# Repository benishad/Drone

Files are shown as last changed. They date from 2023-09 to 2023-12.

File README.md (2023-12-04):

## ✈️드론의 비행 거리를 늘려보자[중계 통신 드론 프로젝트]
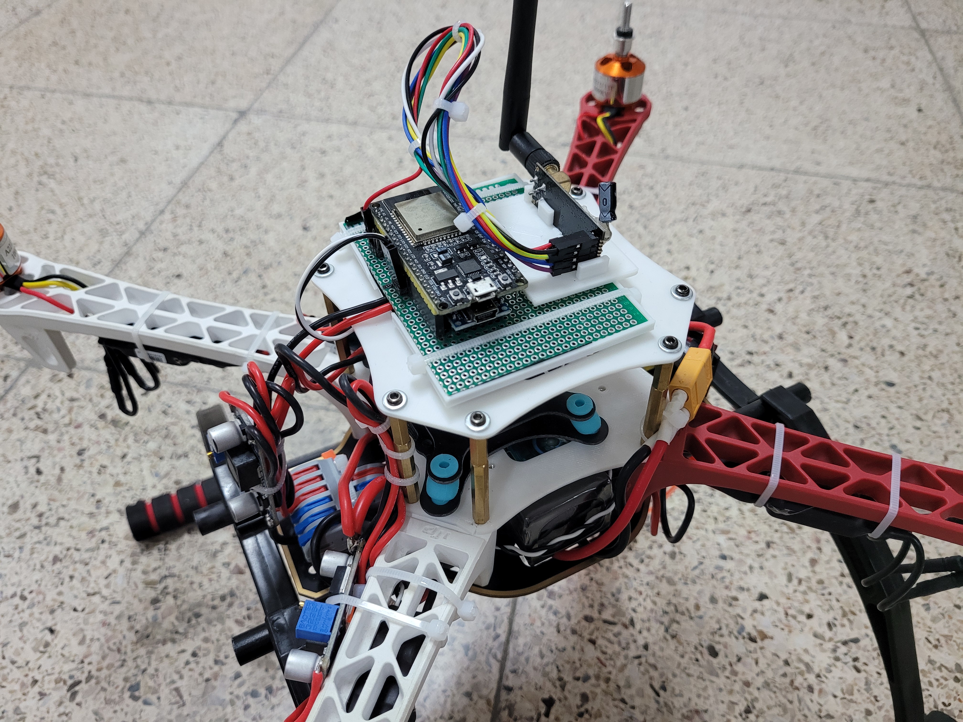
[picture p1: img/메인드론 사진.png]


## 중계 통신 드론이란?

- **중계 드론**은 일반 학생들이 저렴하게 드론을 제작하고 SW코딩 학습과 더불어 드론의 비행 거리를 늘리는데 목적이 있습니다.

- 중계 통신을 이해하기 쉬운 예는 휴대전화 입니다. 저희가 상대방과 전화를 할 수 있는 이유는 기지국이 중계소 역할을 해주는 덕분입니다.

- 조종기와 드론 사이에 중계소 역할을 하는 드론을 제작하는 것이 중계 드론 프로젝트 입니다.

- 드론 시뮬레이터를 제작하여 문서에서 제작한 조종기를 사용하여 드론 조종 훈련이 가능합니다.

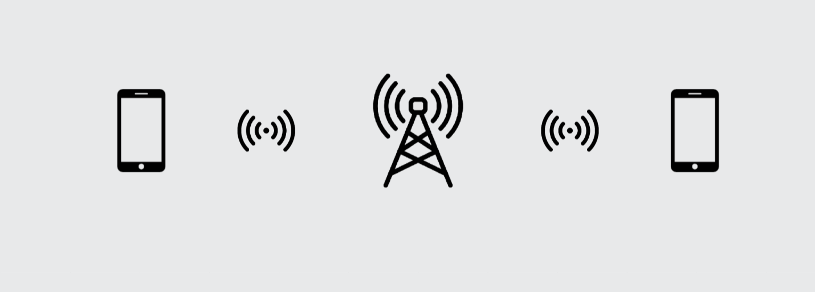
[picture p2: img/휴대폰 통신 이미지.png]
휴대폰_통신_이미지 휴대전화 통신 방식
<br>

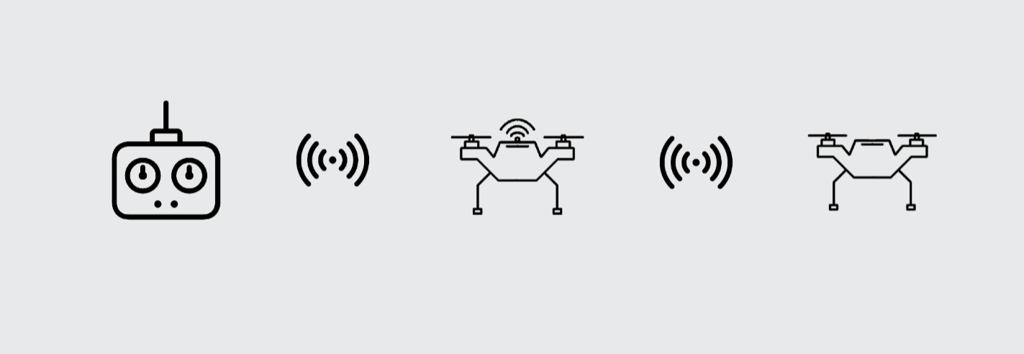
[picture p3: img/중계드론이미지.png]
중계드론이미지 중계 통신 드론 방식


## 바로가기
1. [중계 통신 드론이란?](#중계-통신-드론이란)

2. [바로가기](#바로가기)
    - [준비물](#준비물)
    - [회로도](#회로도)
    - [드론 제작에 앞서](#드론-제작에-앞서)
    - [제작 과정](#제작-과정)
    - [문서](#문서)

3. [중계 드론 빌드 방법 PDF](https://drive.google.com/file/d/1Zqlsaz8OV26cVhaoOtoAvIVqaOmRjo3B/view?usp=sharing)

4.  [드론 시뮬레이터 다운로드](https://drive.google.com/file/d/1ymEPB1GEQYfEJyJiITfJfxDNSJ_VvF2R/view) 설정 방법은 문서를 참고
 
<br>

## 준비물
>준비물 예시 입니다. 방식만 같거나 비슷하다면 다른 더욱 좋은 솔루션이 있을 수 있습니다.

### 준비
- ESP32 **(필수)**
- ATmega328 **(필수)**
- Nrf24l01 **(필수)**
- 10μF커페시터(안전성을 높여줍니다.)
- GY-521(MPU6050) **(필수)**
- 스텝다운 모듈 혹은 레귤레이터
- 조이스틱 혹은 조종기(조종기는 내부를 제거하고 조이스틱을 사용합니다. 고장난 조종기를 추천) **(필수)**
- 토글 스위치 **(필수)**
- 헤더 핀 소켓
- 3mm 인서트 너트
- 진동 방지용 댐퍼 **(필수)**
- F450 드론 프레임 **(필수)**
- 모터와 ESC (ESC용량에 주의해 주세요.) **(필수)**
- 배터리와 프롭 **(필수)**

혹은 다른 프레임을 준비해도 괜찮습니다. 또한, 폴더에 F450 규격에 프레임 출력 파일이 있습니다. 높은 추력과 효율을 위해서는 모터, 배터리, 프롭을 고려해 알맞은 제품을 구해야 합니다. **문서에서는 효율에 대한 내용을 다루지 않습니다.**

<br>

## 회로도
  >회로는 조종기, 중계 드론, 메인 드론 3가지 입니다.

### 조종기
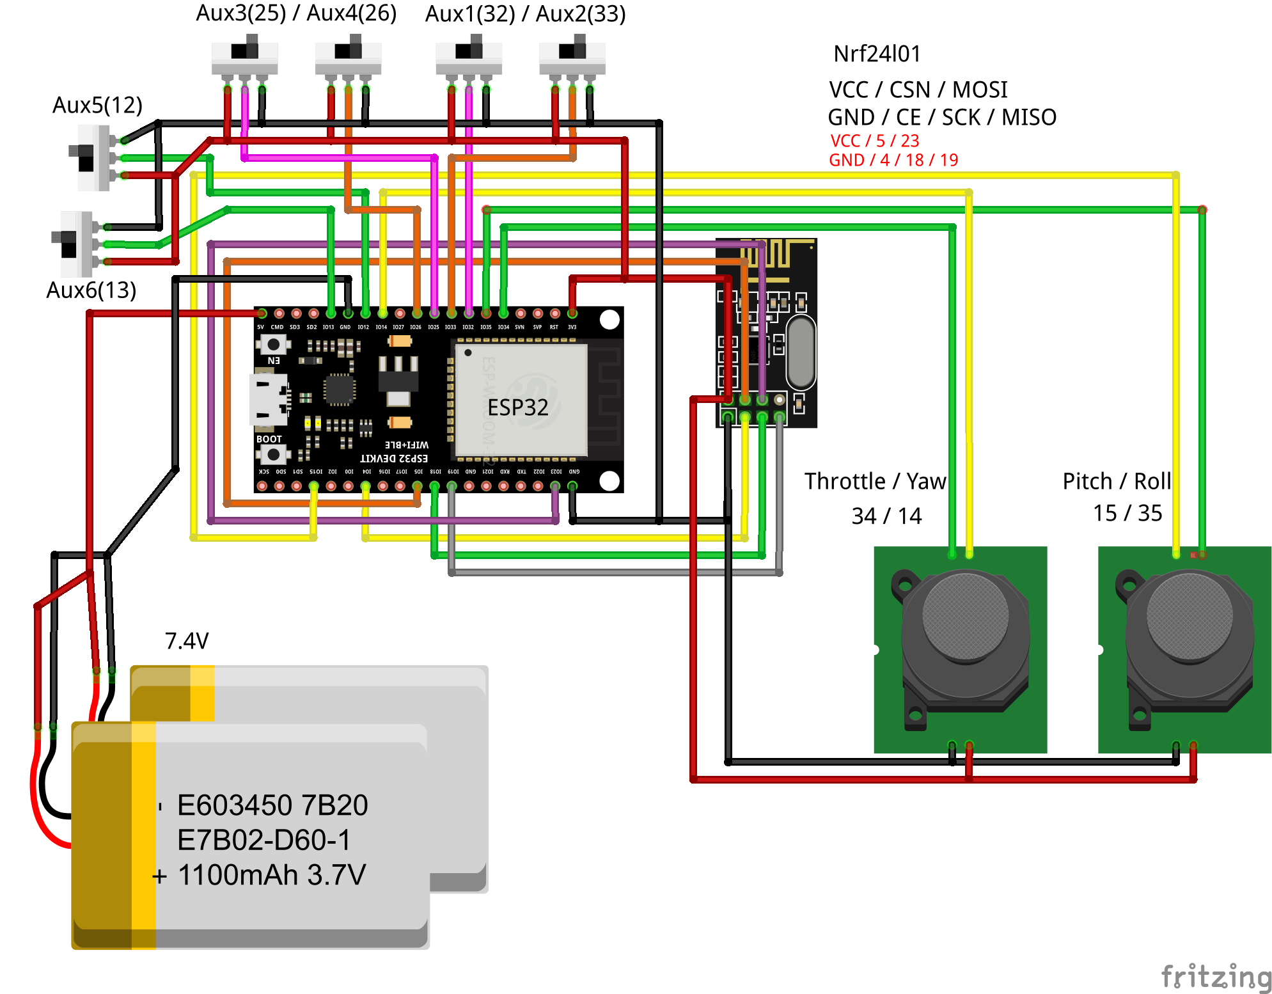
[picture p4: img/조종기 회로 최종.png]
조종기_회로 조종기 회로
<br>

### 중계 드론
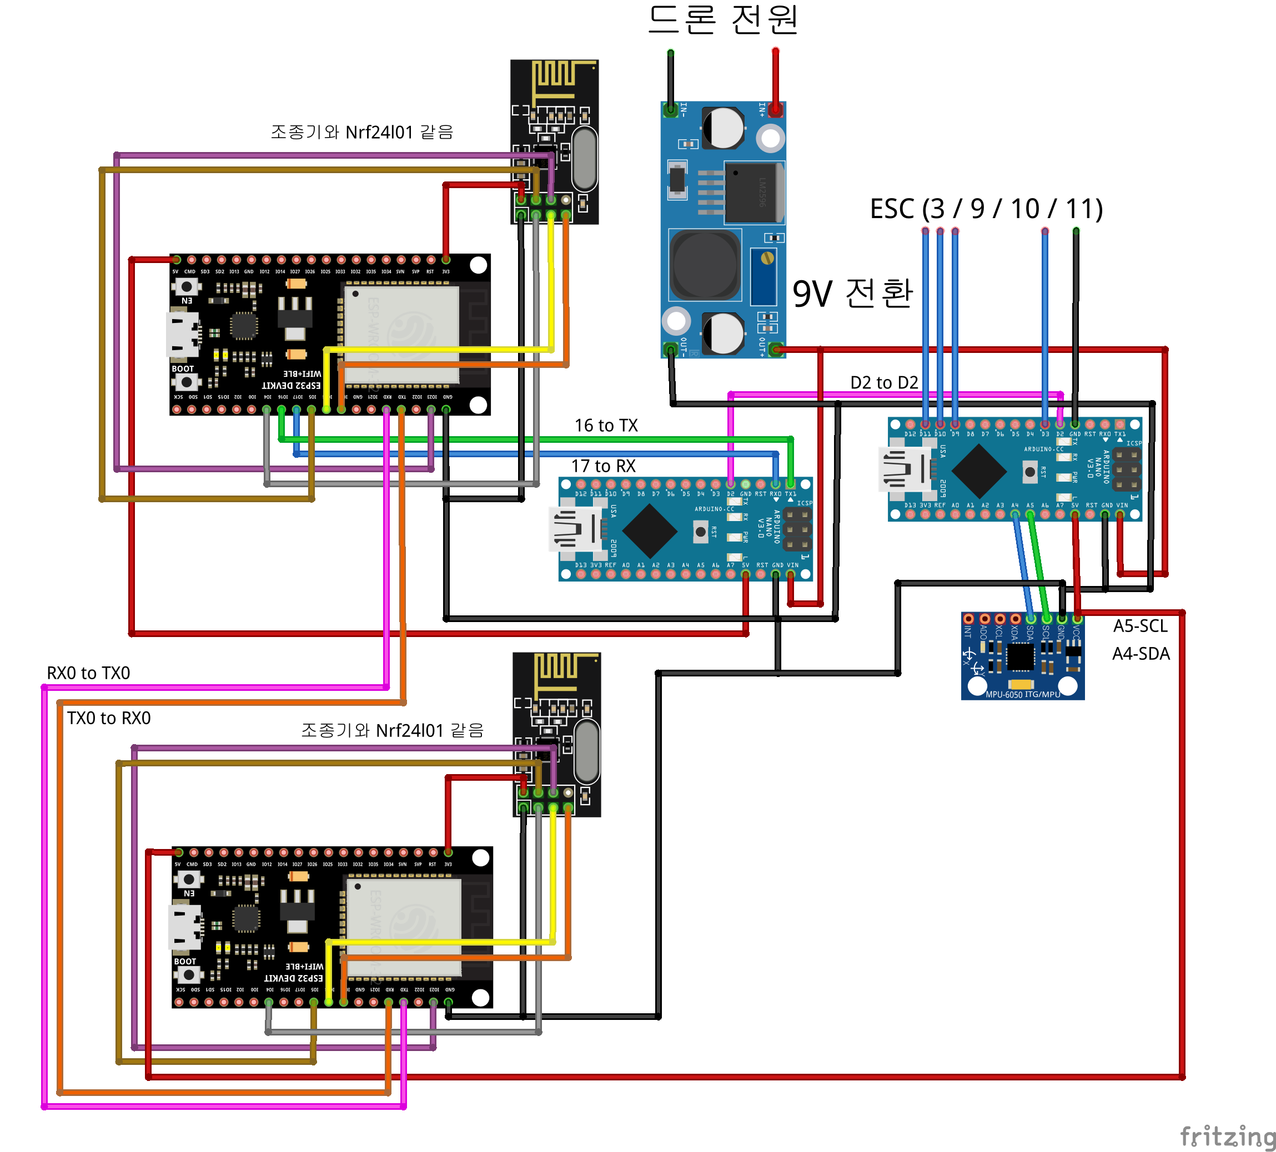
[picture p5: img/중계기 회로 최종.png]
중계기_회로 중계기 회로
<br>

### 메인 드론
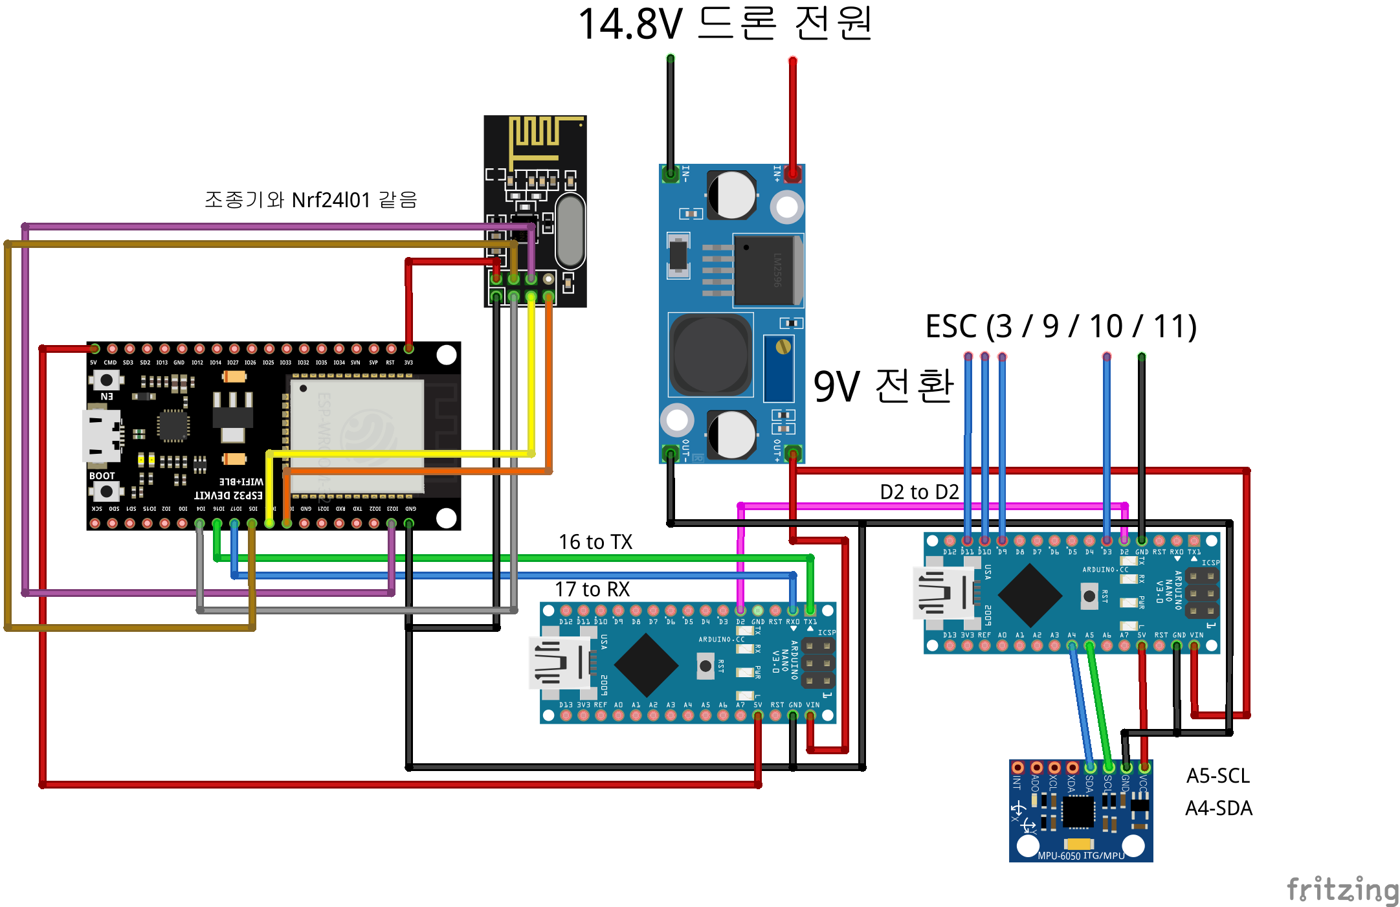
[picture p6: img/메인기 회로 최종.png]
<br>

### 시뮬레이터 수신기
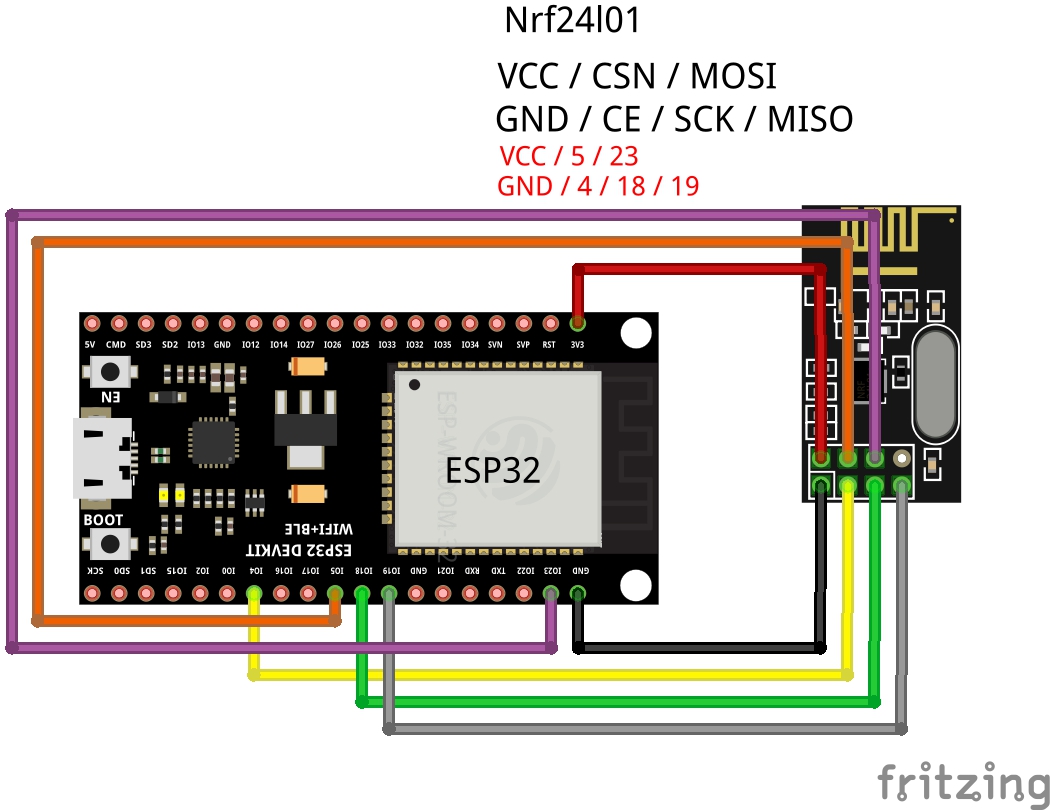
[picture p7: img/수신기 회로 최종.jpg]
<br>
수신기는 위에 제작한 중계 드론과 메인 드론 회로와 동일합니다. 따라서 두 드론 중 하나를 사용하여 소스코드를 업로드하는 것으로 시뮬레이터 수신기로 사용이 가능합니다.

<br>

## 드론 제작에 앞서
  - ### 전압 분배
    ESP32와 아두이노 보드 전원공급을 드론 배터리로 해결 합니다. 따라서 드론의 14.8V 혹은 다른 용량의 배터리 전압을 낮춰줄 필요가 있습니다. 위 회로에서는 9V로 정하였지만 **사용하는 보드에 입력 전압을 숙지하고 그에 맞춰서 조정**하길 바랍니다.
  <br>
  <br>
  배터리 전원은 ESC, ESP32, 아두이노 등으로 전달 되어야 하기에 적절한 분배 장비를 이용해야 합니다.<br><br>
  
&nbsp;&nbsp;&nbsp;&nbsp;&nbsp;&nbsp;&nbsp;&nbsp;&nbsp;&nbsp;- 전원 분배 보드

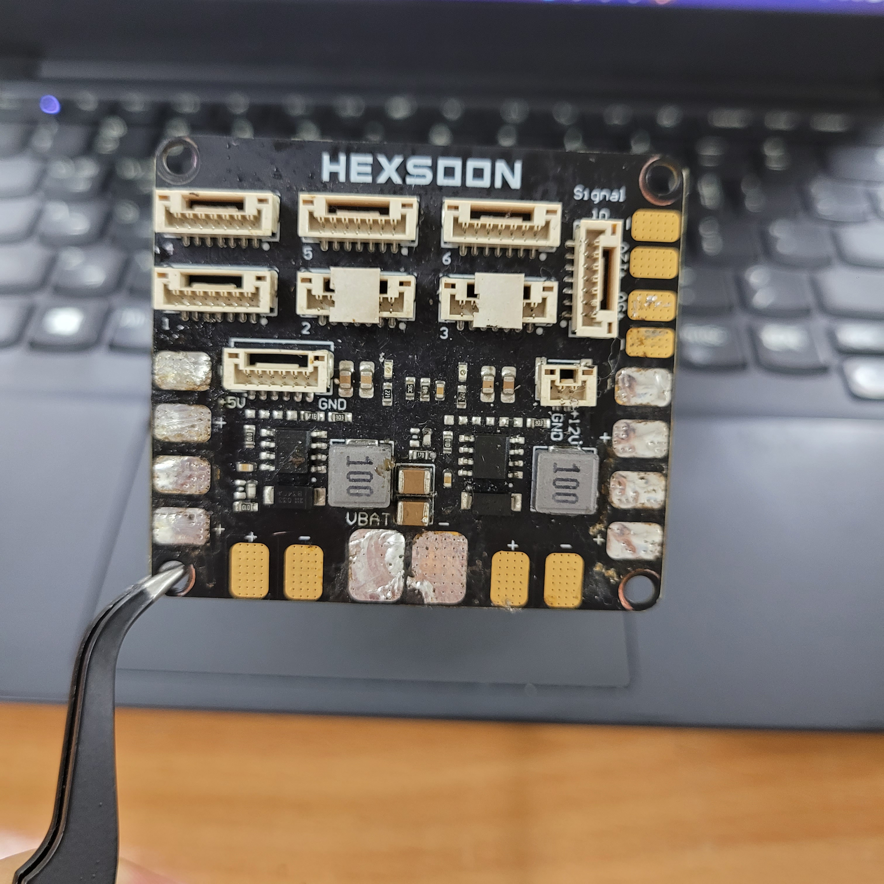
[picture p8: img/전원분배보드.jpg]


  &nbsp;&nbsp;&nbsp;&nbsp;&nbsp;&nbsp;&nbsp;&nbsp;&nbsp;&nbsp;- 바디 전원 분배

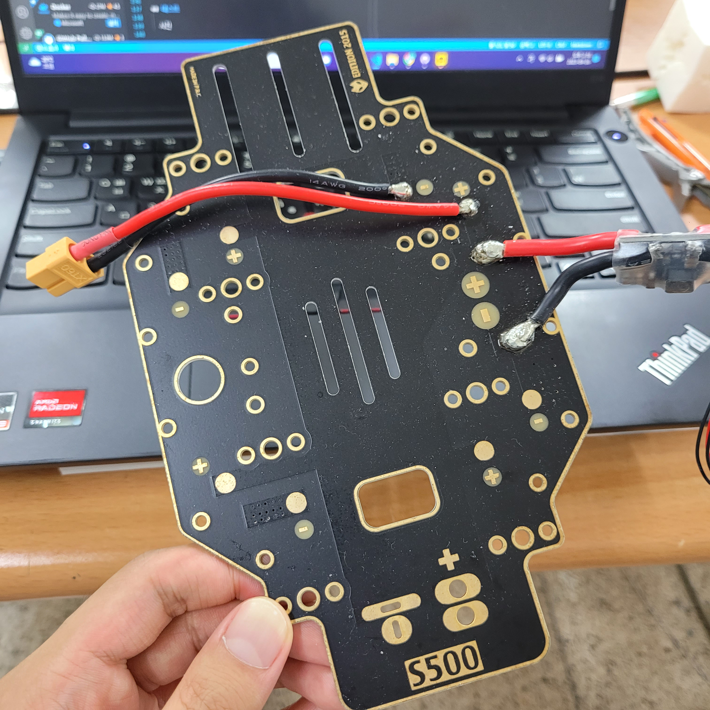
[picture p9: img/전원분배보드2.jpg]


  &nbsp;&nbsp;&nbsp;&nbsp;&nbsp;&nbsp;&nbsp;&nbsp;&nbsp;&nbsp;- 기타 등등...

  - ### 전압 조정
    전압 조정 방법 또한 여러 방법이 있습니다.
    <br>
    BEC, 레귤레이터, 스텝다운 등등..
    <br>
    이 문서에서는 스텝다운 모듈을 사용하여 전압을 낮추어 아두이노 보드에 입력합니다.<br>
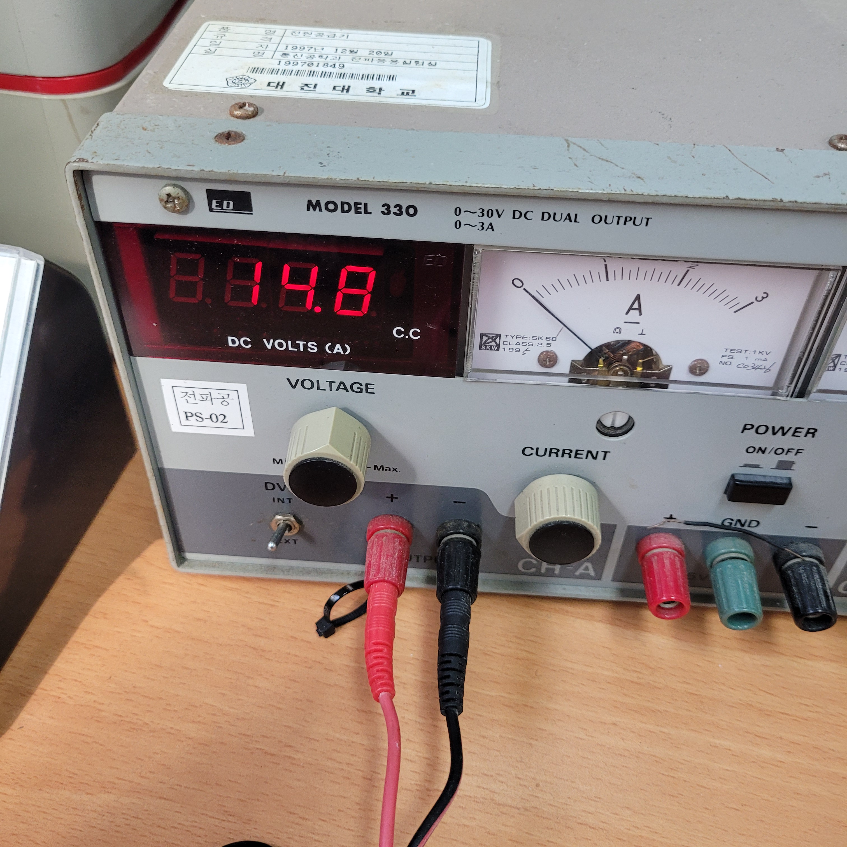
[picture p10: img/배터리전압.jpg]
    <br>

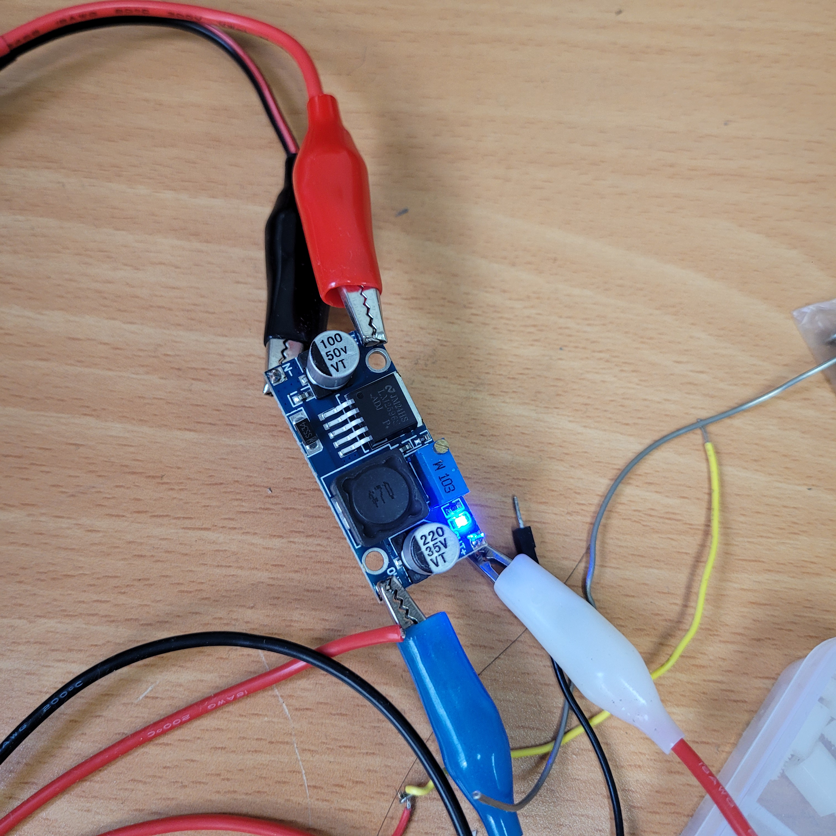
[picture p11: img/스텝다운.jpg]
    <br>

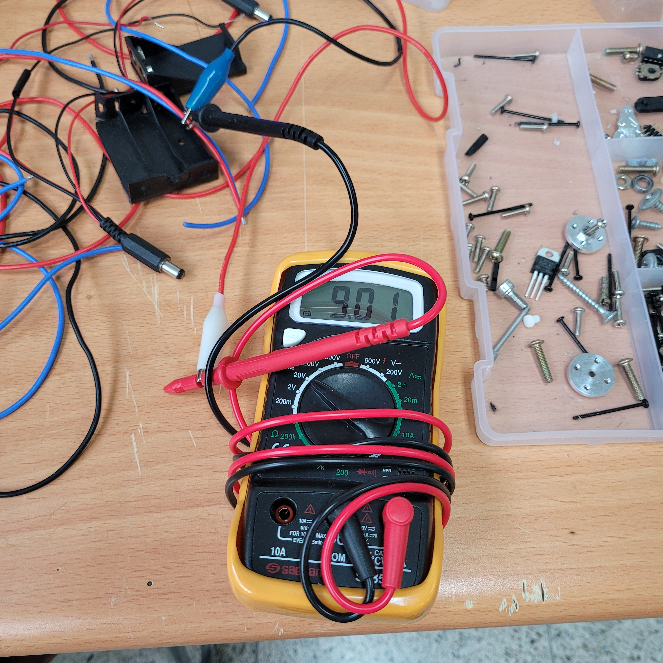
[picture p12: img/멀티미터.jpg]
    
  
  <br>

  - ### Multiwii
    Multiwii는 드론 제작에 많이 사용되는 FC(Flight Controller) 소프트웨어입니다.
    Multiwii는 오픈 소스 프로젝트로서, 사용자들이 자유롭게 소스 코드를 수정하거나 개선할 수 있습니다. 개인적인 프로젝트부터 상업적인 제품까지, 다양한 범위에서 사용될 수 있습니다.<br>
    아래 링크를 통해 Multiwii를 다운로드하여 사용합니다.
  <br>
  <br>

    [Multiwii 다운로드](http://www.multiwii.com/) 바로가기

  <br>
  <br>
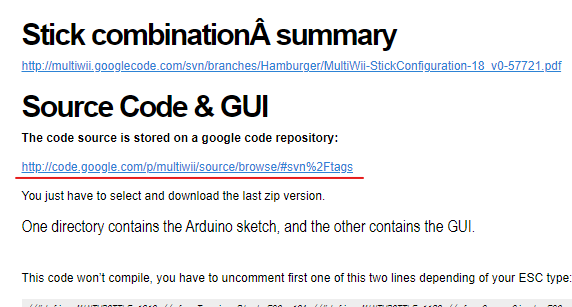
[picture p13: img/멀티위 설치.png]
  <br><br>

## 제작 과정

  - ### ESP32와 Nrf24l01 10μF커패시터 납땜
    >필수는 아니지만 편의성과 안정성을 위해서 진행하는 것을 추천합니다.<br>

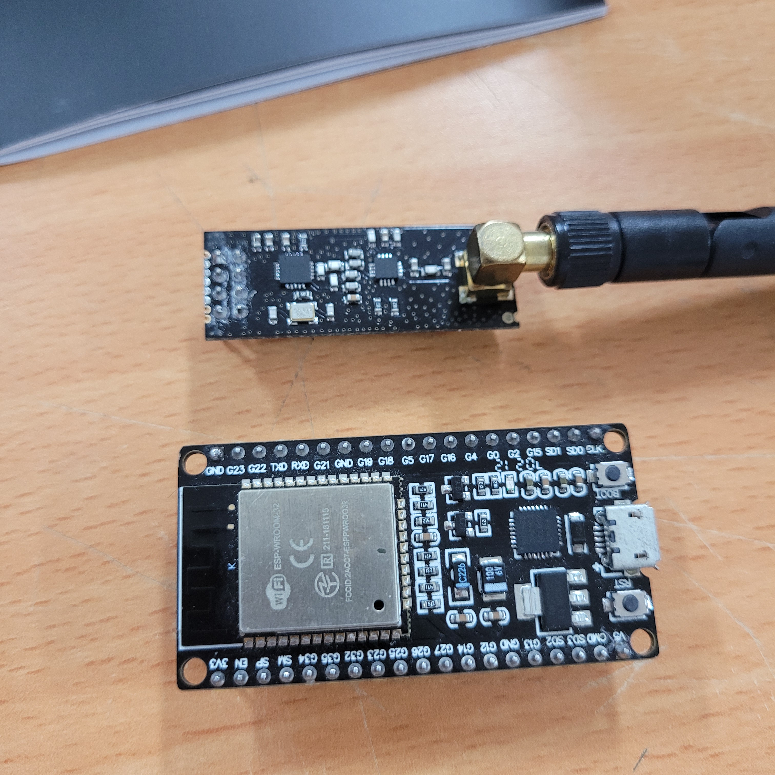
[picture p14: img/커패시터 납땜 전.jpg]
    <br>

    - 커패시터 납땜 위치를 확인하세요.
    - ESP32 EN 단자와 GND를 연결해야 합니다.<br>

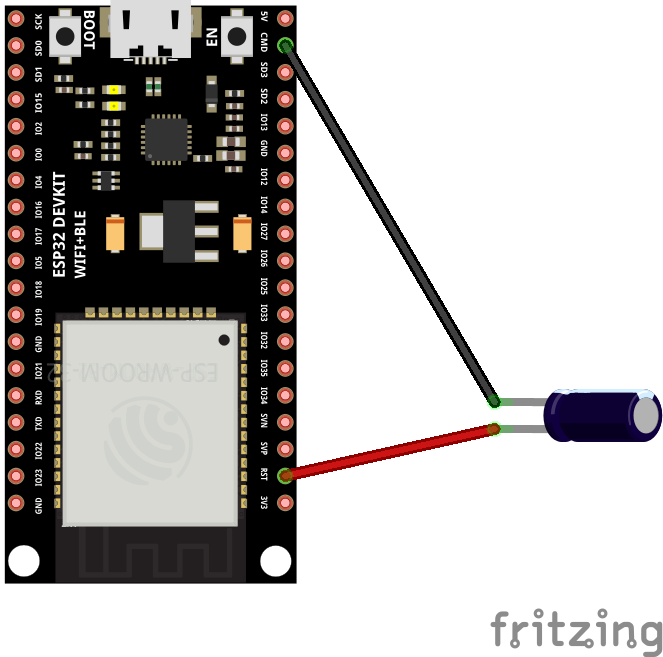
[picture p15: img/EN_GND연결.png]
    <br>

    - 위 처럼 연결해도 괜찮지만 너무 단자가 길어집니다. 여기서는 아래와 같이 직접 연결을 하여 공간을 최소화 하겠습니다.<br>

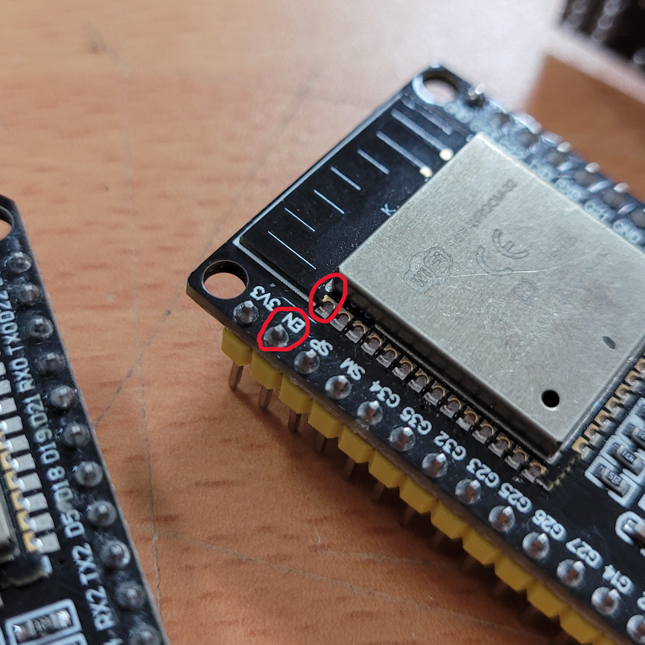
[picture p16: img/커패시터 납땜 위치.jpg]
    <br>

    - 커패시터 단자 + - 를 확인하세요.<br>

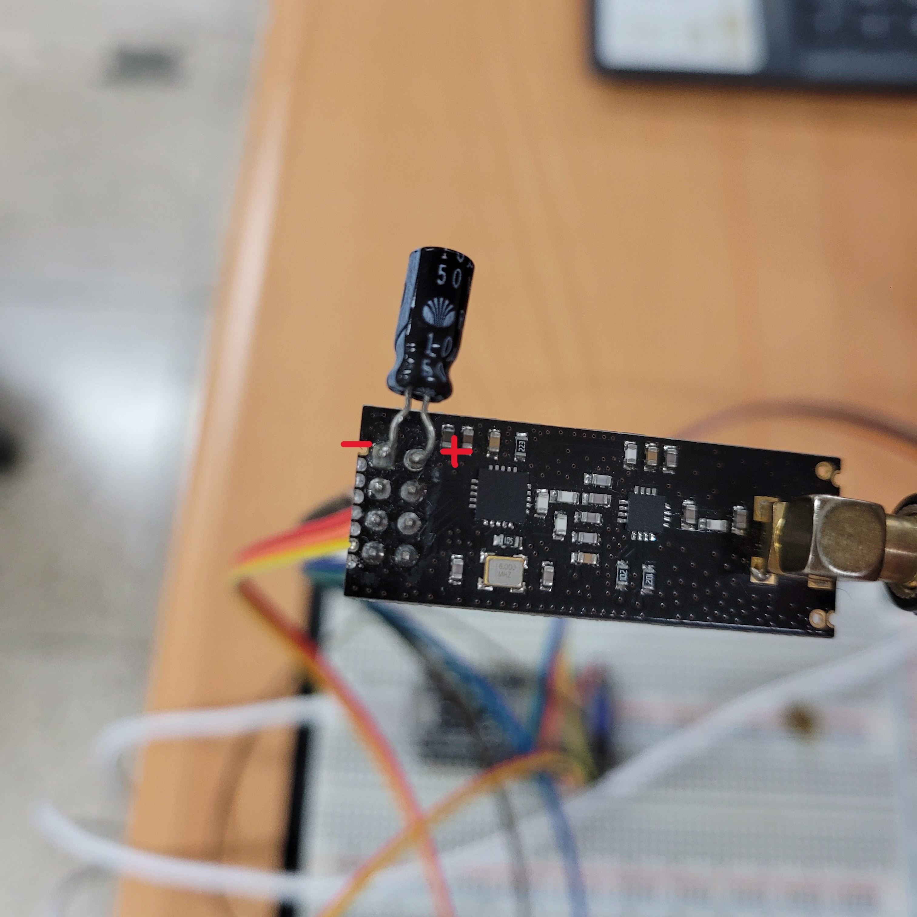
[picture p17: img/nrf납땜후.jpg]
    <br>
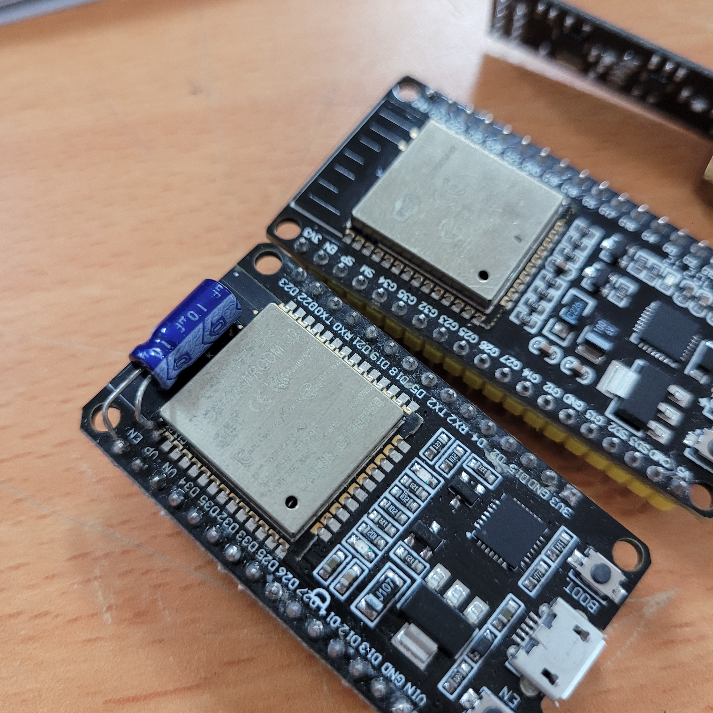
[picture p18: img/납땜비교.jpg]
    <br>

    - 위 와 같은 모습을 만들었으면 성공입니다. 다시 언급하지만 위와 똑같이 진행 할 필요는 없습니다.<br>

  - ### 조종기 제작
    
    조종기 제작은 두 가지 방법이 있습니다.

    1. 실제 조종기 혹은 고장난 조종기 기판을 제거하고 사용하기.

    2. 브레드보드 혹은 만능기판에 회로를 구성하여 사용하기.

    회로도를 위에 게시해 두었으니 회로 제작은 넘어가겠습니다.
    아래는 제작된 조종기 두 가지 버전입니다.

    #### 조종기 ver.1
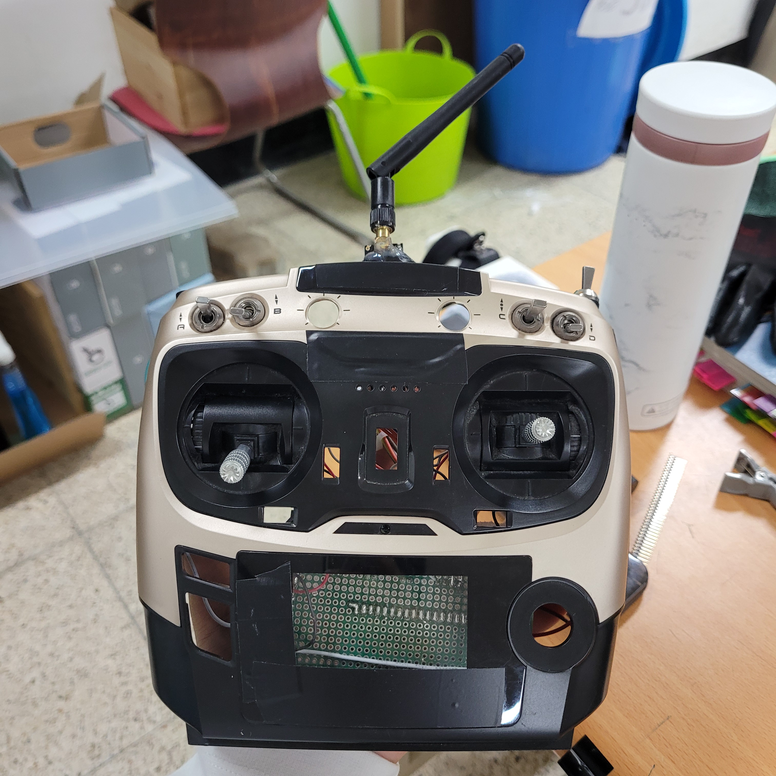
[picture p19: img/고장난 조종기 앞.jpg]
    <br>

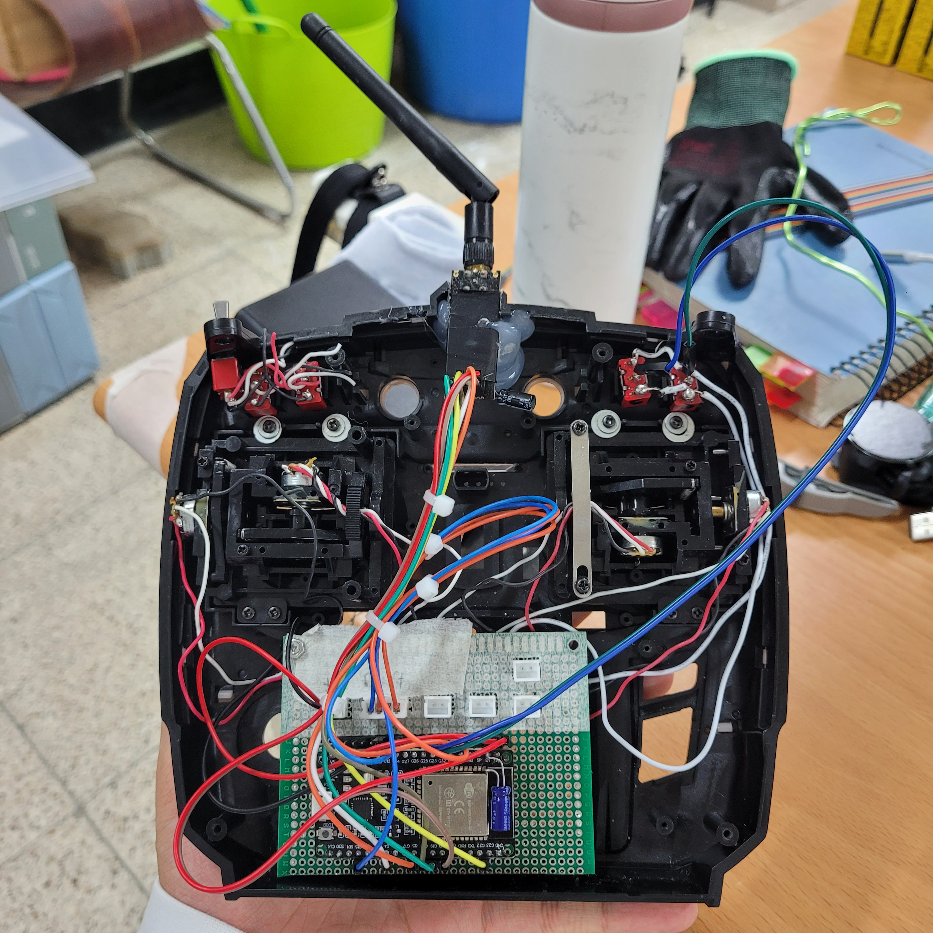
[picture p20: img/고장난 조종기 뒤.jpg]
    <br>

    #### 조종기 ver.2
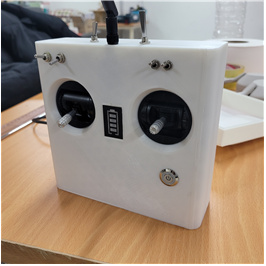
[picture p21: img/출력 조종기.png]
    <br>

  - ### MPU6050 설치 과정
    mpu6050은 수평을 유지시키기 위한 핵심 부품 입니다. 비행시 mpu6050에 문제가 생기지 않게 댐퍼와 출력물을 사용해 mpu6050을 고정해야 합니다.

    재료를 준비합니다.<br>
    CAD폴더에서 mpu6050 관련 출력물을 출력해 사용합니다. 직접 설계하거나 다른 방법을 사용해도 괜찮습니다. **mpu6050에 이상이 생기지 않게 하는 작업임을 인지해 주세요.**

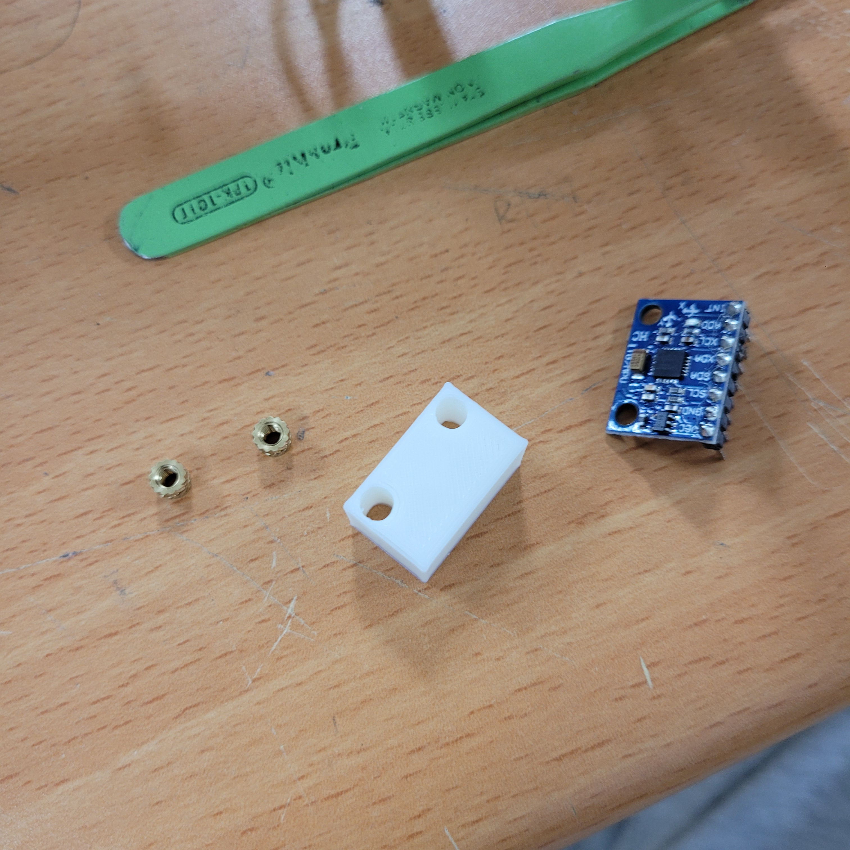
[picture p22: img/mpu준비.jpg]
    

    ※ 해당 출력물은 헤더소켓을 끼웠을 때 고정되는 길이로 제작되었습니다.<br>
    인서트 너트를 넣고 조립 준비를 합니다.

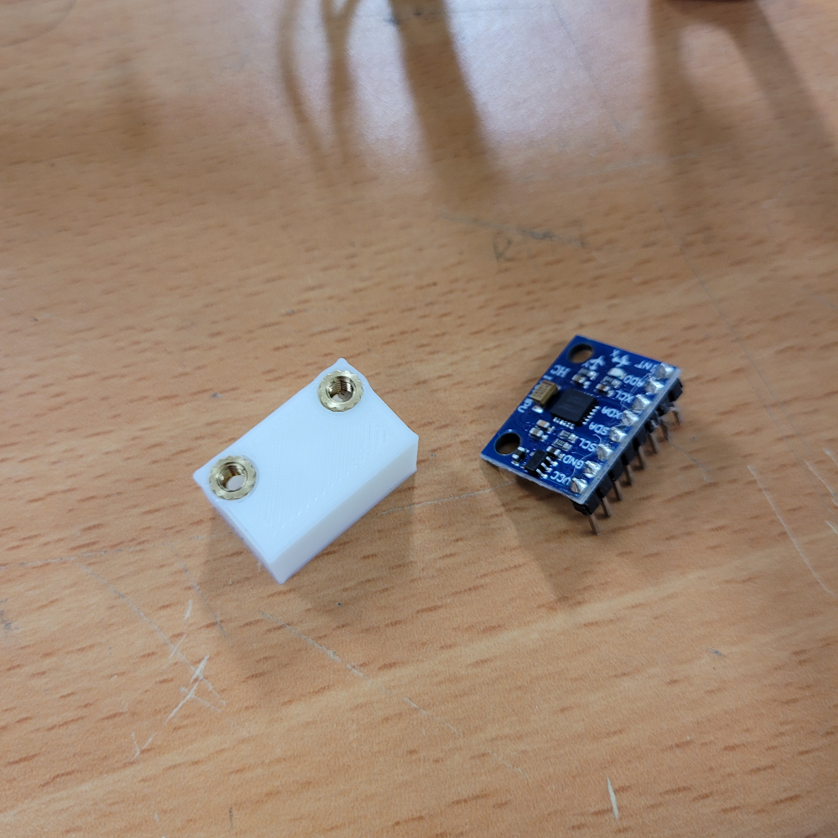
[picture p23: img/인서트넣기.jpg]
    

    비행시 생기는 진동에 대비하도록 댐퍼 위에 mpu6050을 설치하여 마무리 합니다.

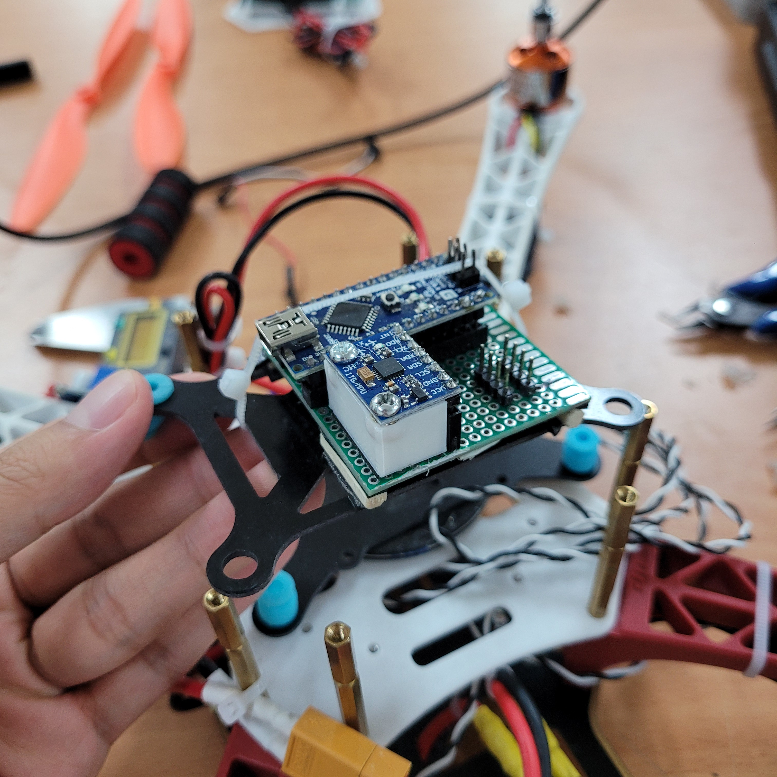
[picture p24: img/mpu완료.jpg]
    

<br>

## 문서

  이후 모든 작업에 대한 설명은 아래 문서에 기술

[중계 드론 빌드 방법 PDF](https://drive.google.com/file/d/1Zqlsaz8OV26cVhaoOtoAvIVqaOmRjo3B/view?usp=sharing)

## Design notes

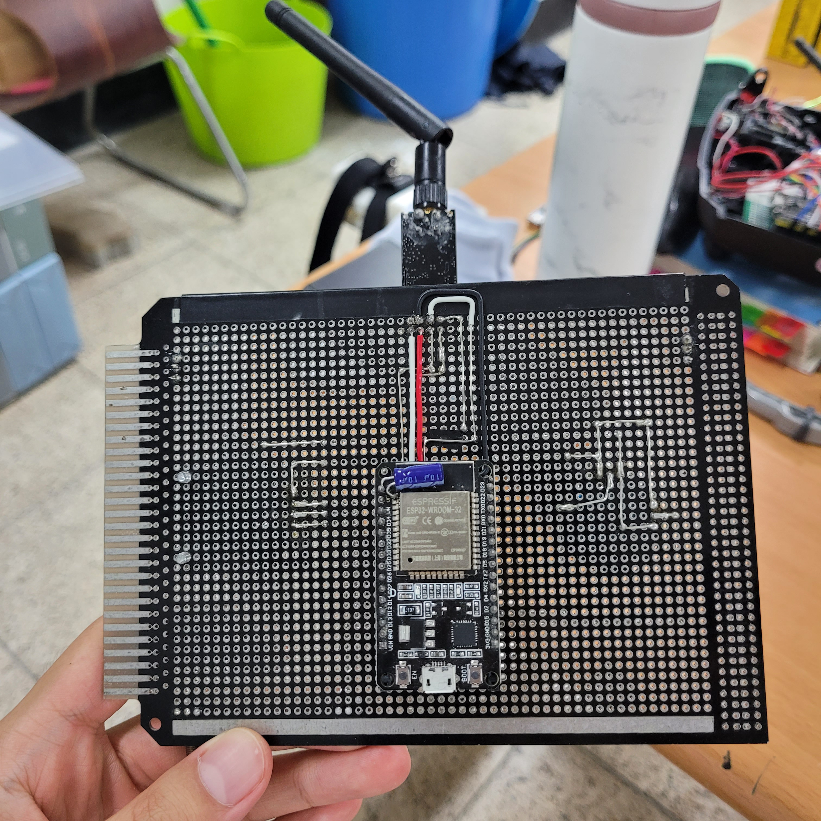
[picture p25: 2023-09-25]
img/기판 조종기 뒤.jpg

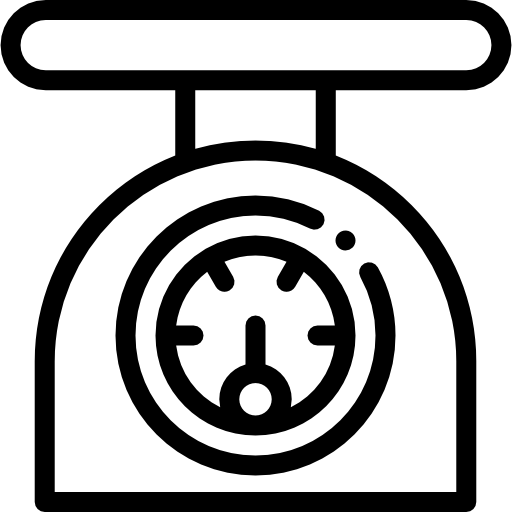
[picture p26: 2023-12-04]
img/무게.png

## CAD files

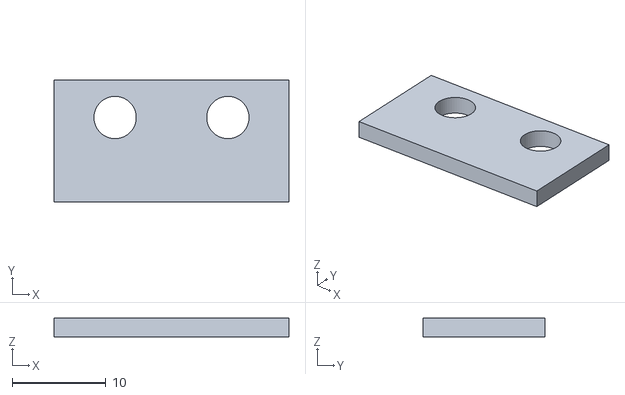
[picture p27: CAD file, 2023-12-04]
CAD/락피스.stl
25.0 x 13.0 x 2.00

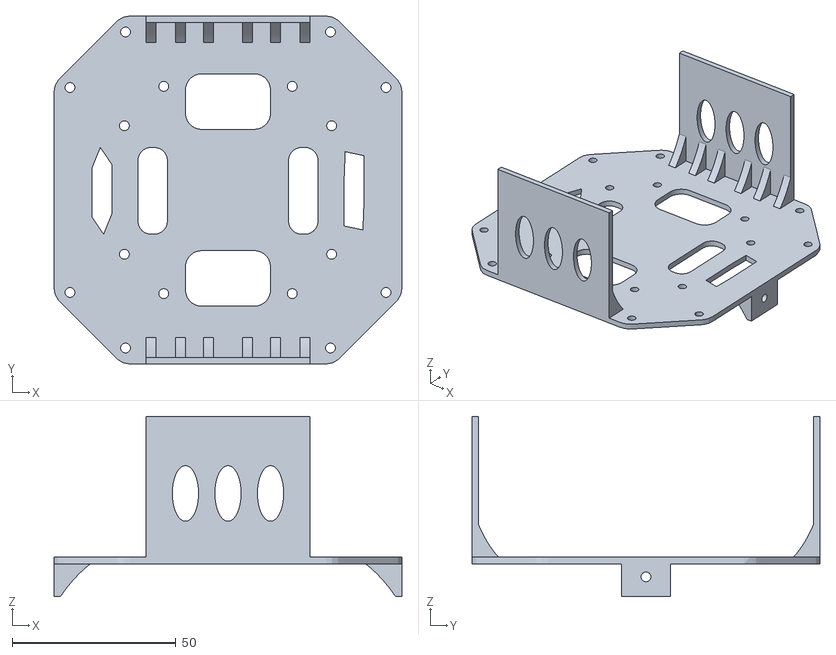
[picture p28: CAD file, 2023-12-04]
CAD/Drone_DOWN.stl
106.3 x 106.3 x 55.0

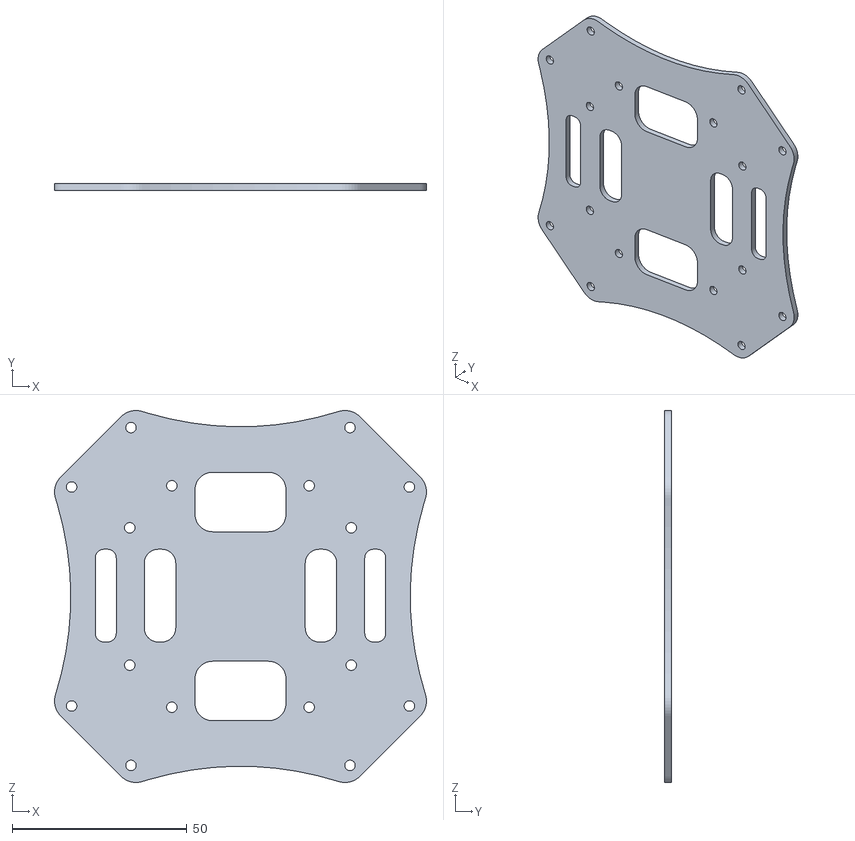
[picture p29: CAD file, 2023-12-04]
CAD/드론 top.STL
106.3 x 2.00 x 106.3

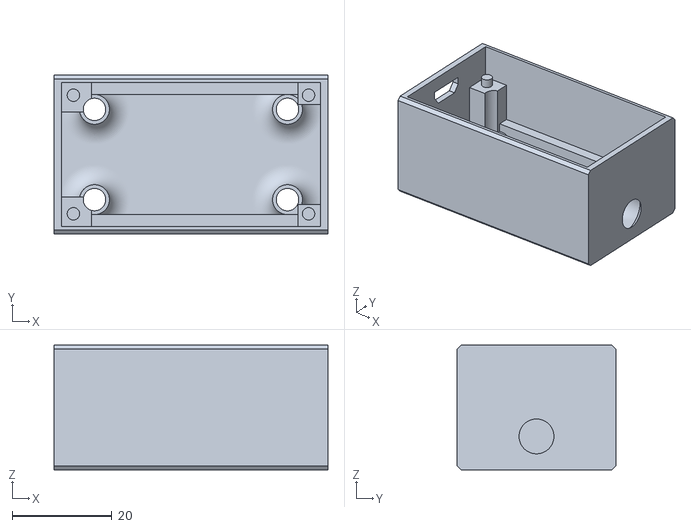
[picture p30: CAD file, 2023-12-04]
CAD/Nrf_Body.stl
55.0 x 32.0 x 25.0

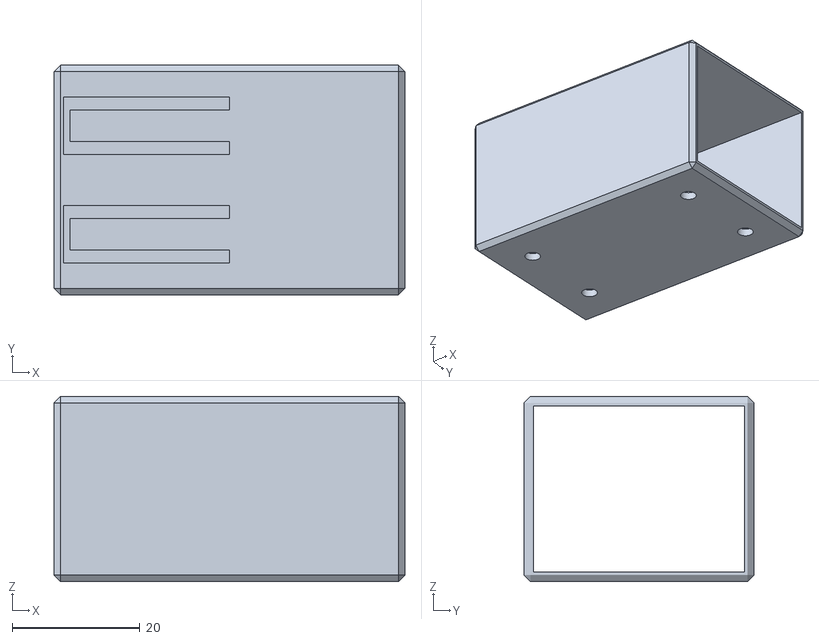
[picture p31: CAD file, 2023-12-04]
CAD/Nrf_Head.stl
55.0 x 36.0 x 29.0

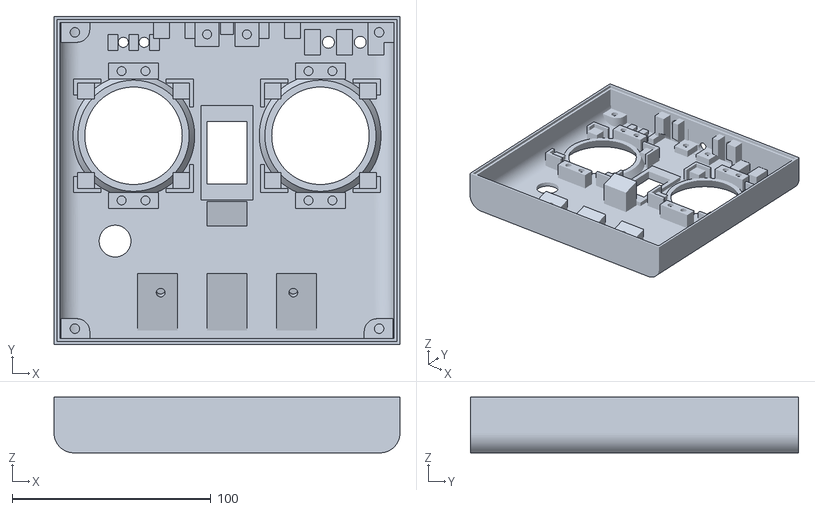
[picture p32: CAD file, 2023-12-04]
CAD/조종기.stl
174.0 x 165.0 x 28.0

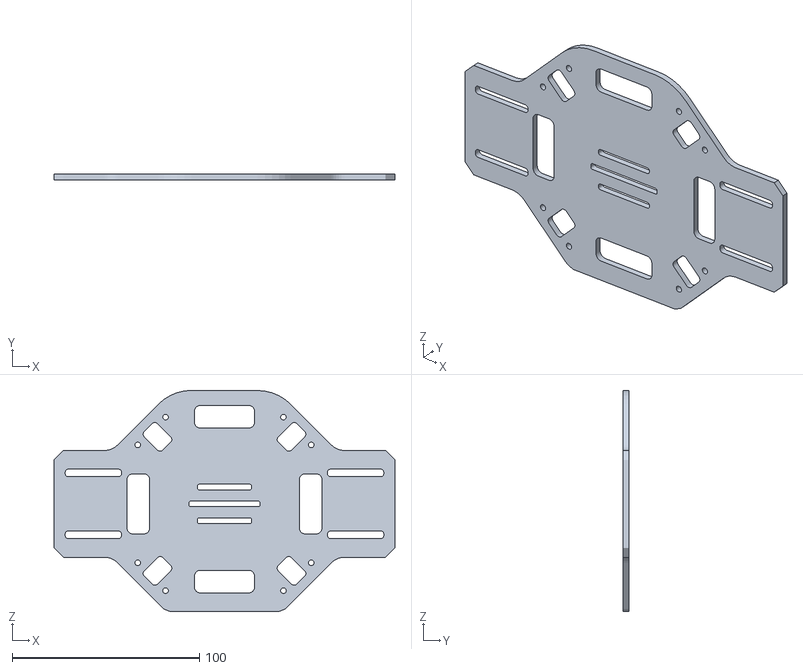
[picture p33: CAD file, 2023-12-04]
CAD/드론 bottom.STL
182.0 x 3.00 x 118.1

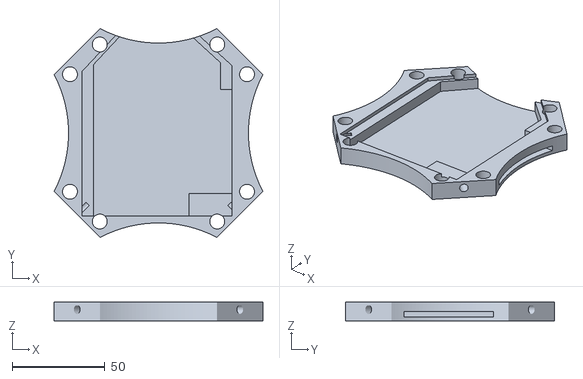
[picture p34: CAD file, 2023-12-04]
CAD/중계드론기판_하단.stl
112.4 x 112.4 x 10.0

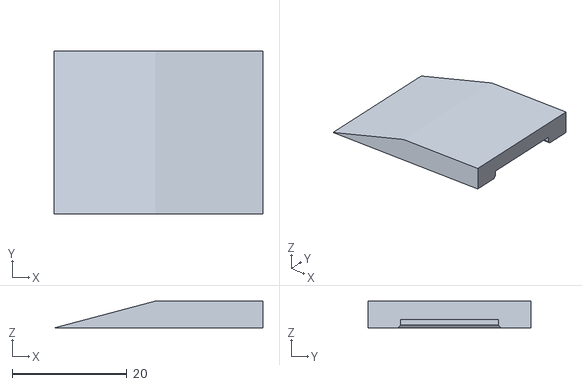
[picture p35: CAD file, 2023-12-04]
CAD/bracket.stl
36.4 x 28.4 x 4.70

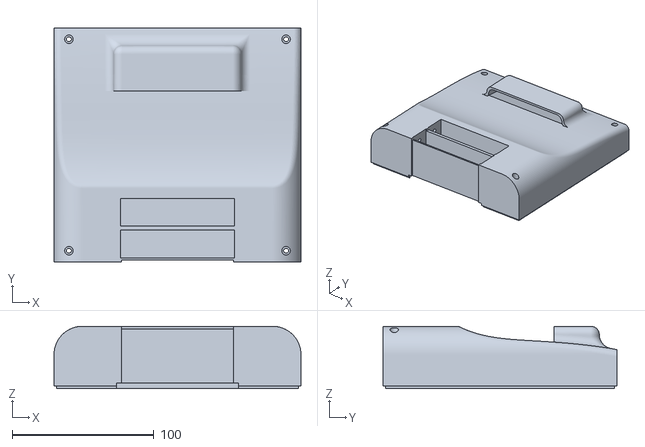
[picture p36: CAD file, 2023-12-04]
CAD/조종기 플레이트.stl
174.0 x 165.0 x 44.0

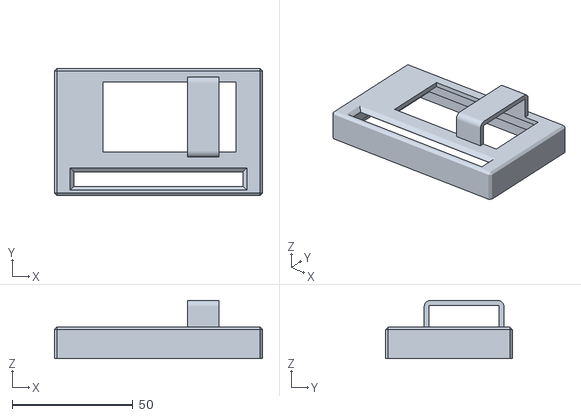
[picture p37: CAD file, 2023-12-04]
CAD/메인 드론 케이스_1.stl
86.0 x 52.5 x 24.0

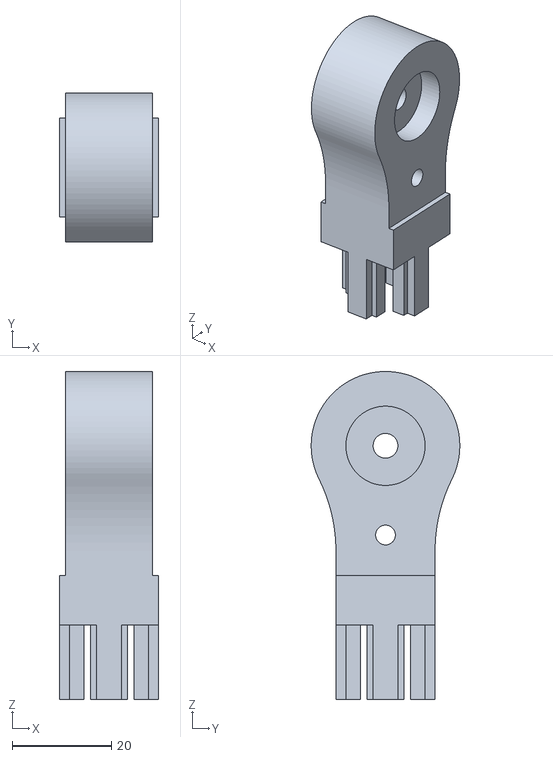
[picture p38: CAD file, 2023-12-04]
CAD/수평계 마운트.stl
20.0 x 30.0 x 66.2

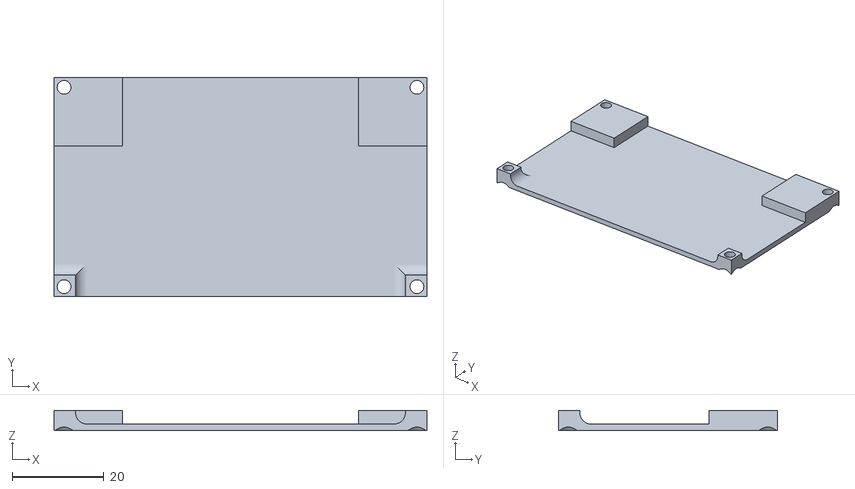
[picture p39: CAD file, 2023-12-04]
CAD/메인 드론 케이스_2.stl
81.4 x 47.9 x 4.45

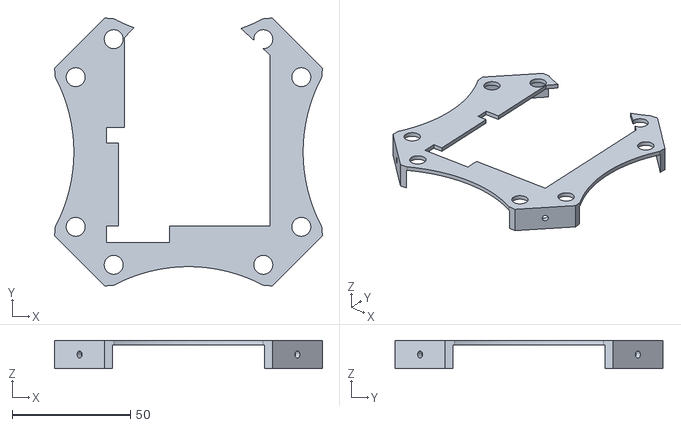
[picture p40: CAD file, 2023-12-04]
CAD/중계드론기판_상판.stl
113.1 x 113.1 x 12.0

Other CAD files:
CAD/수평계.stl
CAD/Drone_UP.stl
CAD/nrf24_hw.stl
CAD/mpu_leg.stl

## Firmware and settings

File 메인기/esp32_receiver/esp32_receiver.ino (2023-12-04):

//////////////////////////////////////////////////////////////////////////////////
//메인 드론
//중계통신으로 받은 값으로 작동하는 메인 드론 ESP32.
//받은 값을 처리하여 다시 나노로 전송하는 역할을 한다.
#include <SPI.h>
#include <RF24.h>

#define RXp2 16   //uart통신을 위한 핀
#define TXp2 17   //uart통신을 위한 핀

//long long pipeIn = 0x1234ABCDEFLL;   //주소값 설정
const uint64_t pipeIn = 0x5A1B2C3D4E5F6A7BLL;

char buf[10]; //  

RF24 radio(4, 5); // GPIO18 for CE, GPIO5 for CSN

bool communicationActive = true;  // 통신 활성화 상태
unsigned long lastCommunicationTime = 0;
unsigned long communicationTimeout = 5000;  // 통신 타임아웃 시간 (5초)

// 안전한 착지를 위한 Roll, Pitch, Yaw 값
const byte safeRoll = 128;
const byte safePitch = 128;
const byte safeYaw = 128;
const byte safeAUX1 = 000;
const byte safeAUX2 = 001;
const byte safeAUX3 = 000;
const byte safeAUX4 = 000;
const byte safeAUX5 = 000;
const byte safeAUX6 = 001;

struct MyData {
  byte throttle;
  byte yaw;
  byte pitch;
  byte roll;
  byte AUX1;
  byte AUX2;
  byte AUX3;
  byte AUX4;
  byte AUX5;
  byte AUX6;
};

MyData receivedData;
MyData lastData;  // 마지막으로 받은 데이터를 저장할 변수

const int charge = 14;
const int fire = 12;

void setup() 
{
  Serial.begin(115200);
  Serial2.begin(9600, SERIAL_8N1, RXp2, TXp2);    //Atmega와 uart통신을 위한 시리얼
  radio.begin();
  radio.openReadingPipe(1, pipeIn); // Set the same address used in the transmitter
  radio.setDataRate(RF24_2MBPS);  // 데이터 전송 속도 설정
  // RF24_250KBPS, RF24_1MBPS, RF24_2MBPS
  //radio.setPALevel(RF24_PA_HIGH);
  //거리가 가까운 순으로 RF24_PA_MIN / RF24_PA_LOW / RF24_PA_HIGH / RF24_PA_MAX 등으로 설정
  radio.startListening(); //수신모드

  pinMode(charge, OUTPUT);
  pinMode(fire, OUTPUT);
}

void loop() 
{
  if (radio.available()) 
  {
    radio.read(&receivedData, sizeof(MyData));
    lastCommunicationTime = millis();  // 통신이 성공한 경우 타임아웃 타이머 재설정

    //============================================================
    //=====================메인 드론 개별 정지========================

    if(receivedData.AUX4 == 1) 
    {
      lastData.yaw = 127; // 중간값으로 설정
      lastData.pitch = 127;
      lastData.roll = 127;
      lastData.AUX1 = 0;
      lastData.AUX2 = 1;
      lastData.AUX5 = 0;
      lastData.AUX6 = 1;
      sendToNano(lastData);
      serial_print(lastData);
    } 
    else 
    {
      lastData = receivedData;  // 통신 데이터를 lastData에 저장
      sendToNano(receivedData);
      serial_print(receivedData);
    }
    
    //==============================================================
    //==============================================================

    //============================================================
    //===================== 코일건 발사 코드 ========================
    if(receivedData.AUX5 == 1)
    {
      Serial.println("- 충전 -");
      digitalWrite(charge, HIGH);
    }
    else if(receivedData.AUX5 == 0)
    {
      Serial.println("- 충전 꺼짐 -");
      digitalWrite(charge, LOW);
    }
    
    if(receivedData.AUX6 == 0)
    {
      digitalWrite(fire, HIGH);
      Serial.println("발사");
    }
    else if(receivedData.AUX6 == 1)
    {
      digitalWrite(fire, LOW);
      Serial.println("발사꺼짐");
    }
    //==============================================================
    //==============================================================
    
    communicationActive = true;
    delay(10);
  }
  
  //안전모드 동작부분
  else 
  {
    // 통신이 끊겼을 때의 동작
    if (communicationActive && (millis() - lastCommunicationTime >= communicationTimeout)) 
    {
      communicationActive = false;  // 통신 끊김 상태로 설정
      // 스로틀 값을 천천히 감소시켜 안전한 착지 모사
      for (int throttleValue = receivedData.throttle; throttleValue >= 0; throttleValue -= 2) 
      {
        Serial2.print("A");
        sprintf(buf, "%03d", throttleValue);
        Serial2.print(buf);
        Serial2.print("B");
        Serial2.print(safeYaw);  // 안전한 Yaw 값
        Serial2.print("C");
        Serial2.print(safePitch);  // 안전한 Pitch 값
        Serial2.print("D");
        Serial2.print(safeRoll);  // 안전한 Roll 값
        Serial2.print("E");
        sprintf(buf, "%03d", safeAUX1);
        Serial2.print(buf);
        Serial2.print("F");
        sprintf(buf, "%03d", safeAUX2);
        Serial2.print(buf);
        Serial2.println("G");
        delay(1000);  // 100ms 간격으로 스로틀 값을 감소시킴
      }
    }
  }
}

void sendToNano(MyData data) 
{
    Serial2.print("A");
    sprintf(buf, "%03d", data.throttle);
    Serial2.print(buf);
    Serial2.print("B");
    sprintf(buf, "%03d", data.yaw);
    Serial2.print(buf);
    Serial2.print("C");
    sprintf(buf, "%03d", data.pitch);
    Serial2.print(buf);
    Serial2.print("D");
    sprintf(buf, "%03d", data.roll);
    Serial2.print(buf);
    Serial2.print("E");
    sprintf(buf, "%03d", data.AUX1);
    Serial2.print(buf);
    Serial2.print("F");
    sprintf(buf, "%03d", data.AUX2);
    Serial2.print(buf);
    Serial2.println("G");
}
void serial_print(MyData data)
{
  Serial.print("메인기 =>  Throttle: ");
  Serial.print(data.throttle);
  Serial.print("  Yaw: ");
  Serial.print(data.yaw);
  Serial.print("  Pitch: ");
  Serial.print(data.pitch);
  Serial.print("  Roll: ");
  Serial.print(data.roll);
  Serial.print("  AUX1: ");
  Serial.print(data.AUX1);
  Serial.print("  AUX2: ");
  Serial.print(data.AUX2);
  Serial.print("  AUX3: ");
  Serial.print(data.AUX3);
  Serial.print("  AUX4: ");
  Serial.print(data.AUX4);
  Serial.print("  AUX5: ");
  Serial.print(data.AUX5);
  Serial.print("  AUX6: ");
  Serial.println(data.AUX6);
}

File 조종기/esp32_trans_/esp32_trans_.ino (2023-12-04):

//조종기 ESP32
//조종기에는 조이스틱 두개와 토글 스위치 5개, 푸쉬 버튼 1개가 설치됨
#include <SPI.h>
#include <RF24.h>

const uint64_t pipeOut = 0xABCD1234567890EFLL;  //주소값 설정

RF24 radio(4, 5); // 4번 ce 5번 csn

//조이스틱 핀 할당
const int THR = 34;
const int YAW = 14;
const int PITCH = 15;
const int ROLL = 35;
//각종 버튼 핀 할당
const int SW1 = 32;
const int SW2 = 33;
const int SW3 = 25;
const int SW4 = 26;
const int SW5 = 12;
const int SW6 = 13;

struct MyData {   //전송할 데이터 구조체 생성
  byte throttle;
  byte yaw;
  byte pitch;
  byte roll;
  byte AUX1;
  byte AUX2;
  byte AUX3;
  byte AUX4;
  byte AUX5;
  byte AUX6;
};

MyData data;

void resetData() 
{
  data.throttle = 0;
  data.yaw = 127;
  data.pitch = 127;
  data.roll = 127;
  data.AUX1 = 0;
  data.AUX2 = 0;
  data.AUX3 = 0;
  data.AUX4 = 0;
  data.AUX5 = 0;
  data.AUX6 = 0;
}

void setup()
{
  Serial.begin(115200);
  radio.begin();
  //radio.setAutoAck(false);
  //radio.setDataRate(RF24_250KBPS);
  // RF24_250KBPS, RF24_1MBPS, RF24_2MBPS
  //radio.setPALevel(RF24_PA_HIGH);
  //거리가 가까운 순으로 RF24_PA_MIN / RF24_PA_LOW / RF24_PA_HIGH / RF24_PA_MAX 등으로 설정
  radio.openWritingPipe(pipeOut);
  radio.stopListening(); // 송신모드
  resetData();

  pinMode(SW1, INPUT);    //angle 모드
  pinMode(SW2, INPUT);    //horizon 모드
  pinMode(SW3, INPUT);    //중계 단일 호버링 모드
  pinMode(SW4, INPUT);    //메인 단일 호버링 모드
  //응용 핀
  pinMode(SW5, INPUT);    //코일건 충전
  pinMode(SW6, INPUT);    //코일건 발사
}

/**************************************************/
//조이스틱에 중간 값이 조이스틱마다 저항 값에 차이가 있어서 그 값을 맞춰주는 함수
int mapJoystickValues(int val, int lower, int middle, int upper, bool reverse)
{
  val = constrain(val, lower, upper);
  if (val < middle)
    val = map(val, lower, middle, 0, 128);
  else
    val = map(val, middle, upper, 128, 255);
  return (reverse ? 255 - val : val);
}

void loop()
{
  data.throttle = mapJoystickValues(analogRead(THR), 260, 1890, 4030, false);
  data.yaw      = mapJoystickValues(analogRead(YAW), 0, 2077, 4095, true);
  data.pitch    = mapJoystickValues(analogRead(PITCH), 1179, 1776, 4095, true);
  data.roll     = mapJoystickValues(analogRead(ROLL), 0, 2061, 4095, false);
  data.AUX1     = digitalRead(SW1);
  data.AUX2     = digitalRead(SW2);
  data.AUX3     = digitalRead(SW3);
  data.AUX4     = digitalRead(SW4);
  data.AUX5     = digitalRead(SW5);
  data.AUX6     = digitalRead(SW6);

  radio.write(&data, sizeof(MyData));

  //   송신하는 값을 시리얼 모니터에 출력
  Serial.print("조종기 => ");
  Serial.print("Throttle: ");
  Serial.print(data.throttle);
  Serial.print("  Yaw: ");
  Serial.print(data.yaw);
  Serial.print("  Pitch: ");
  Serial.print(data.pitch);
  Serial.print("  Roll: ");
  Serial.print(data.roll);
  Serial.print("  AUX1: ");
  Serial.print(data.AUX1);
  Serial.print("  AUX2: ");
  Serial.print(data.AUX2);
  Serial.print("  AUX3: ");
  Serial.print(data.AUX3);
  Serial.print("  AUX4: ");
  Serial.print(data.AUX4);
  Serial.print("  AUX5: ");
  Serial.print(data.AUX5);
  Serial.print("  AUX6: ");
  Serial.println(data.AUX6);

////   조이스틱 테스트 코드, 최소 최대 중간 값을 확인하고 수정
//  Serial.print("조종기 => ");
//  Serial.print("Throttle: ");
//  Serial.print(analogRead(THR));
//  Serial.print("  Yaw: ");
//  Serial.print(analogRead(YAW));
//  Serial.print("  Pitch: ");
//  Serial.print(analogRead(PITCH));
//  Serial.print("  Roll: ");
//  Serial.println(analogRead(ROLL));


  //delay(100); // 일정 시간 간격으로 송신 (500ms = 0.5초)
}

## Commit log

2022-02-21 esp32 v.3
2023-03-22 수정
    구문 오류 수정
2023-09-21 drone relay communication(드론 중계 통신)
    드론의 거리 증가를 위한 중계 통신 코드
2023-09-25 Update README.md
    문법 오류 수정
2023-09-25 Update README.md
    이미지 크기 수정
2023-09-25 Update README.md
    이미지 재수정
2023-09-25 Update README.md
    크기 조절
2023-09-25 Update README.md
    이미지 수정
2023-09-25 캐드 첨부
    사진 수정
    [mpu_leg.stl, nrf24_hw.stl]
2023-12-04 Release v.1
    Release v.1
    [Drone_DOWN.stl, Drone_UP.stl, Nrf_Body.stl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]
2023-12-04 수정
    수정
